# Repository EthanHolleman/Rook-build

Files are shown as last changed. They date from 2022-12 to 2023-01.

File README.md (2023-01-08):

# Rook

This is my fork of the GitHub repo for the [Rook](https://github.com/rolohaun/Rook), a mostly 3D printed CoreXY 3D printer designed
by rolohuan. 



Please see his repo for offical build files and other information. I will be using this repository to
log my build of the printer and store any additional / useful files so that they
can be discovered by others who might want to build this printer.

## Part ordering

Went through the Rook [BOM](https://docs.google.com/spreadsheets/d/1oHDEvndkkvPFOBis4atrHRHK_DMTvttFUFWDg2He6To/edit#gid=0) and
ordered everything specified pretty much using all the provided AliExpress links. 

After I made my order I and looking at the CAD files more closely I realized there was no
hardware specified for attaching the Z axis lead screws to the stepper motors. So I
ended up ordering [this flexible couplings from amazon](https://www.amazon.com/AFUNTA-Flexible-Couplings-Compatible-Machines/dp/B07JL1QYLS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).
In the future I'm guessing equivalent AliExpress couplings will be added to the BOM.

## Software

### Klipper

#### Raspberry Pi

The Rpi hosts the Klipper web interface and API.
I am planning on using Klipper running on a RPi Zero V2. I followed the installation
guide [provided by Rolohaun](https://www.youtube.com/watch?v=OmBIHB9TFgc&t=314s)
pretty much to the letter and got my MainSail interface running without
a problem

#### Klipper and MainSail installation

Follow [part II of Rolohuan's Klipper installation guide](https://www.youtube.com/watch?v=-SYqTW7wJTo). The firmware build will be specific to the mainboard that you have selected. I have decided to
use the SKR E3 V3 because this is the board used by Rolohaun in his build. 

#### Local acccess point

Part of the appeal of the Rook to me is its small size which allows it to be extremely portable.
One challenge I anticipate of bringing this thing around to new places is that
there is no physical interface for controling the machine; everything is depedent on being
able to access the Klipper Mainsail interface. This means that the machine needs to be
connected to wifi so I can use a labtop on the same network 
or other device to access the Mainsail interface. This would be problematic in locations
where there is poor or no access to a local network. 

To get around this I am using a Raspberry Pi Pico W as a local access point. Following
[this guide](https://www.recantha.co.uk/blog/?p=21398) from Michael Horne I got my
Pico hosting a local wifi network. Then when I need to connect to the Mainsail interface
and / or work on the Raspberry Pi Zero running Klipper for the Rook I connect
to this local network from my labtop. 

Code I am using for the access point is below.

```python
import socket
import network
from machine import Pin
import time

ssid = "YOUR SSID"
password = "YOUR PASSWORD"
led = Pin("LED", Pin.OUT)

ap = network.WLAN(network.AP_IF)
ap.config(essid=ssid, password=password) 
ap.active(True)

print("Access point active")
print(ap.ifconfig())

while True:
    if ap.active() == True:
        led.on()
    else:
        led.off()
        
    time.sleep(0.1)
```

I then setup my RPi Zero that is actually running klipper to connect to this network when it boots up.
You can use [this guide](https://www.tomshardware.com/reviews/raspberry-pi-headless-setup-how-to,6028.html) to
configure headlesss SSH access.

### Putting things together

First I started by printed out the main components of the frame using Fusion Filaments PLA Pro +.
The Rook is very sensitive to warped parts so I set the bed temp extra high, used a brim
when printing large frame parts and printed the first layer very slow and very hot.

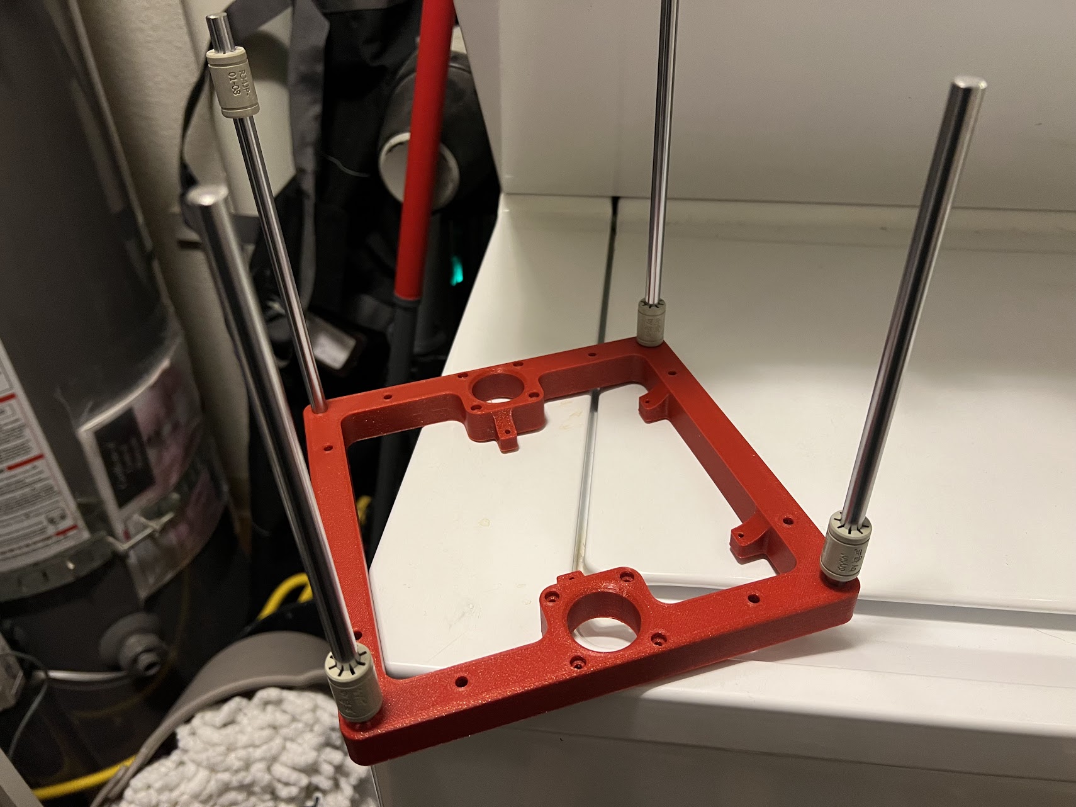
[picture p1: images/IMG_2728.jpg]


With the main frame parts finished I tested the
fit of the linear rods and made sure the delrin
bearings were sliding smoothly along them.



Next I started fitting the rest of the frame and
bed together as well as setting the M3 heat
set inserts using my soldering iron. Everything
went together pretty easily, just make sure all
parts are oriented correctly. I assembled things
backwards at some point. It helps to have the CAD
model open when first putting the frame together
to keep yourself on track as the frame is pretty
symmetrical. 

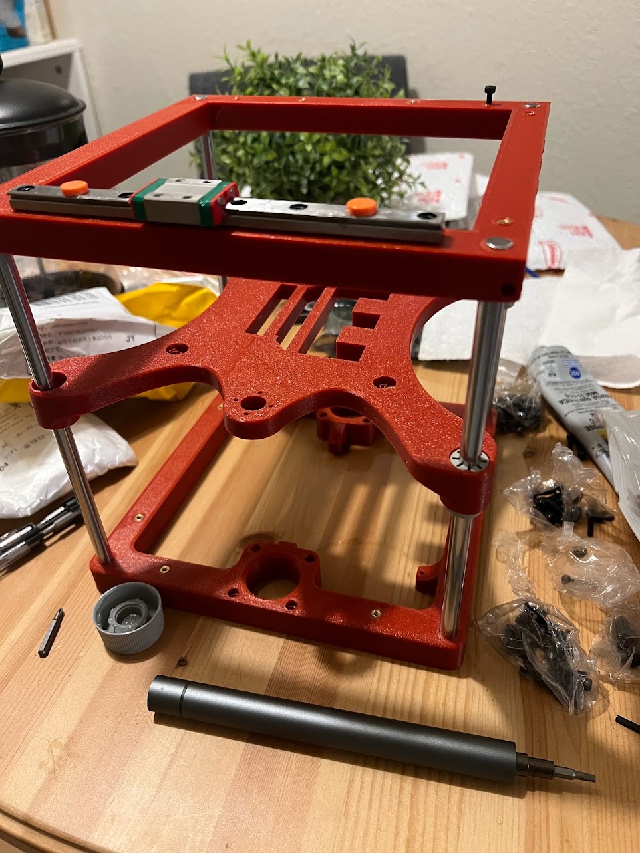
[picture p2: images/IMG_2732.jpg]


I later ended up replacing the bed shown in this
image with the two bearing bedframe that can
be downloaded from Rolohaun's Rook repo. I
found that this bed really does help to reduce
binding on the Z axis. The Rook seems to be very
sensitive to the linear rods not being perfectly
square. The degree of squareness required for a
smooth four bearing set up seems to be difficult
to achieve with 3D printed parts. 

I also lubricated all my linear rods with
Superlube grease by just placing some onto
the rails, moving the rail carriage through the grease
and wiping up the excess. This seemed to work well enough.



Next I printed and assembled the idler towers.
These were a bit tricky to fit everything together.
It helped to sand down the inside area where the washers make contact with the printed plastic with a file. I also used the M5 bolt as a guide to kind of pile the bearings and washers on. As I added more I would screw in the bolt to hold everything in place.

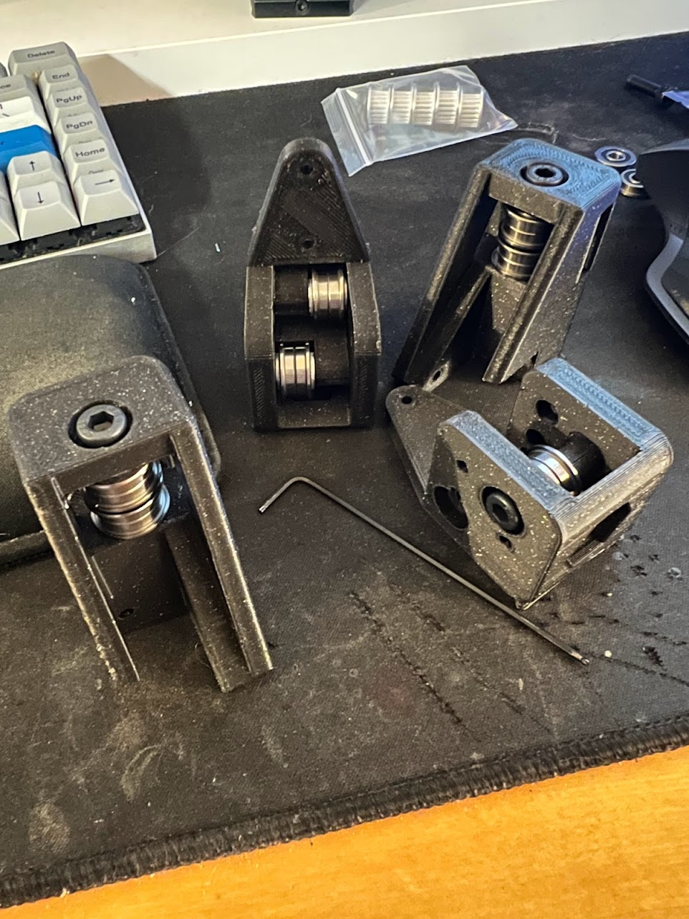
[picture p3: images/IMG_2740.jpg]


With these parts together I then started working on the hot end assembly and the belting. 

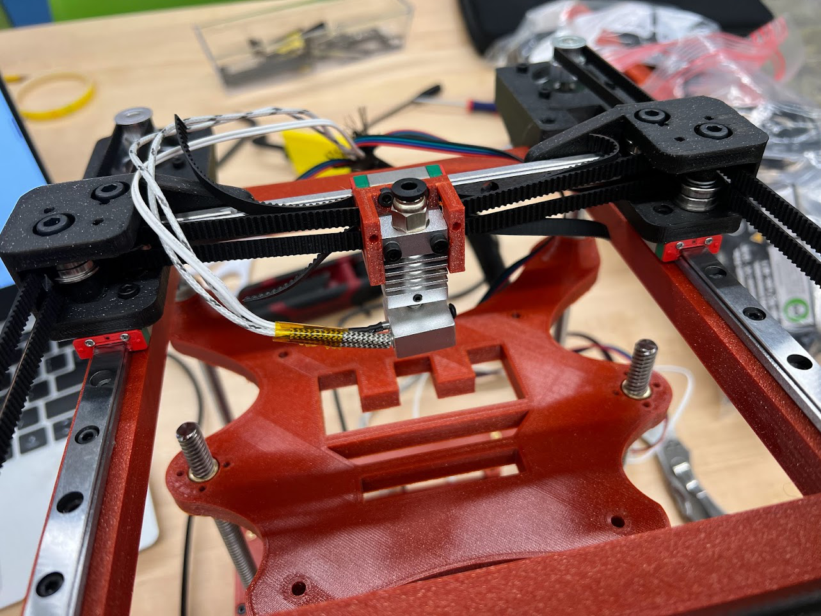
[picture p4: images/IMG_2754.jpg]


I found this image of a general coreXY belting diagram to be very helpful.



After I had the belting figured out I started mounting the bed. I used a 150 mm piece of glass pane I had cut at
a local hardware store with a PEI magnetic build plate as the print surface. 

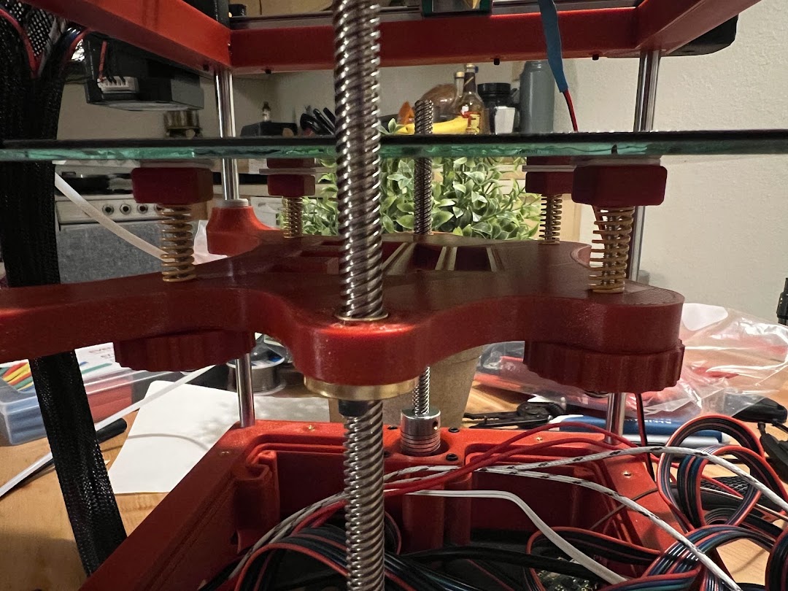
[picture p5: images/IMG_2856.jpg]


I also designed some bed spring tensioning knobs that use the same threaded inserts as the rest of the build.
Double sided tape did not seem like enough to keep the bed attached to the mounts so I just superglued
these to the glass plate.

I then realized that the 40 mm cooling fans I had were too large to fit the hot end mount. So I went into Fusion360 and designed a
mount that would work with my hot end (CR-10 style) and a 40 mm fan. You can download the stl [at this link](https://github.com/EthanHolleman/Rook-build/blob/main/ETH-STLs/X_Carriage-40mm-extra-tall.stl).

Next I moved onto the wiring. I did not want to design a mount for all my individual components so instead I designed an electronics
box that slides into the bottom frame that you can just shove all the wires and computers into and then seal up and never think
about again.

Something to note about this electronics box
is that it needs to be installed *before* you
mount the Z axis motors and the legs because
it will be obstructed and difficult / impossible
to push up from the bottom of the frame otherwise.

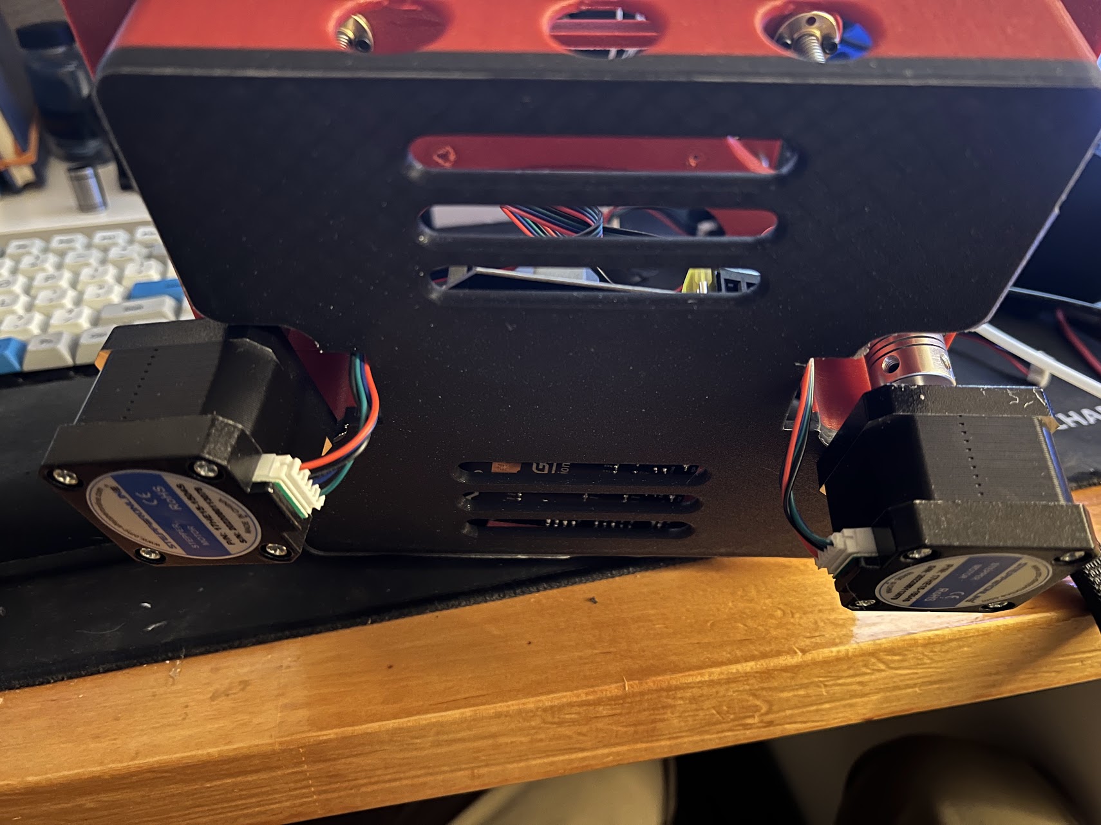
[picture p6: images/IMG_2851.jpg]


Wires for the Z axis motors can be routed
through the holes adjacent to them. 

Everything fits I promise!

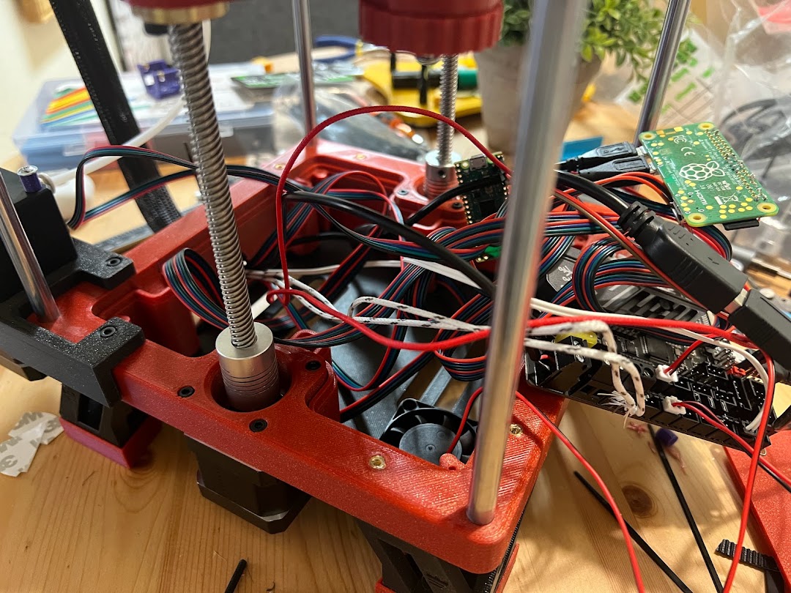
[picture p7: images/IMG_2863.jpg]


After verifying that everything seemed to be working I wired in the cooling fan, did some additional cable management and then sealed everything up using the lid I designed for the electronics box. I also threw in another 40 mm
fan into the enclosure in an attempt to help 
keep things a bit cooler in there. The links for both the box and lid are listed below.

- [Electronics box stl](https://github.com/EthanHolleman/Rook-build/blob/main/ETH-STLs/electronicsBox.stl)
- [Electronics box lid stl](https://github.com/EthanHolleman/Rook-build/blob/main/ETH-STLs/electronicsBoxLid.stl)

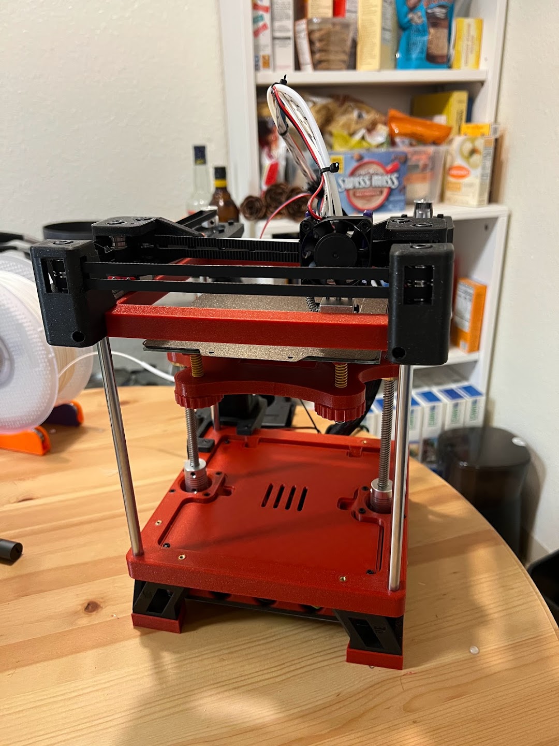
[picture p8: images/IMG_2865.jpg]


The only thing left to do at that point was to mount the part cooling fan and test everything out! After leveling the bed and fooling around
with the Z offset in Klipper I was able to print a calibration cube.

And with that my Rook build was complete. I really enjoyed putting this machine together and feel like I have a much deeper understanding of
3D printers and the mechanics that allow them to function.

[Video of first print](https://www.youtube.com/watch?v=ggh4lNVPjAo)

I posted my Rook to Rolohan's discord server and officially received serial number 27! So this is the 28th Rook to exist in the world (counting starts at 0). Overall this was a very fun project and I would
recommend Rook to anyone looking to try out building
a printer from scratch but does not want to shell
out the cash for a Voron type build. The mostly
3D printed design and relatively low cost to build
(mine came in at around 300 USD when all was said
and done but that could definitely be powered due to
some purchasing inefficiencies on my end) make this
build low risk. An added bonus is that the small
size and light weight means that you can fit
this guy into your second carry on bag no problem.
I fly home for Christmas with mine without any
issue!

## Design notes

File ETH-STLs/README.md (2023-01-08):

# Custom parts

As part of putting Rook together I designed a few parts either to work around
problems I had or to suit my needs for the printer better. They are described
below.

## `electronicsBox.stl` and `electronicsBoxLid.stl`

This is a box and lid that fits into the bottom part of the stock Rook base.
It has pass-throughs for cables so instead of designing mounts for all your
hardware you can just jam everything into this box. I beleive other Rook builders
have published electronics boxes but they do not use the stock bottom frame. 
I had already printed the stock frame so I wanted an electronics box that
would work with that.

## `ExtruderBottomText.stl`

This is a modified X axis motor mount that you can attach to the back left
of Rook to mount the extruder motor cleanly. Mounting the extruder motor at
the bottom of the machine helps to lower the center of gravity.

## `X_Carriage-40mm-extra-tall.stl`

The 40 mm fan was too large to fit on the stock hot end mount so I
modified it to fit this fan size. Seems to work well.

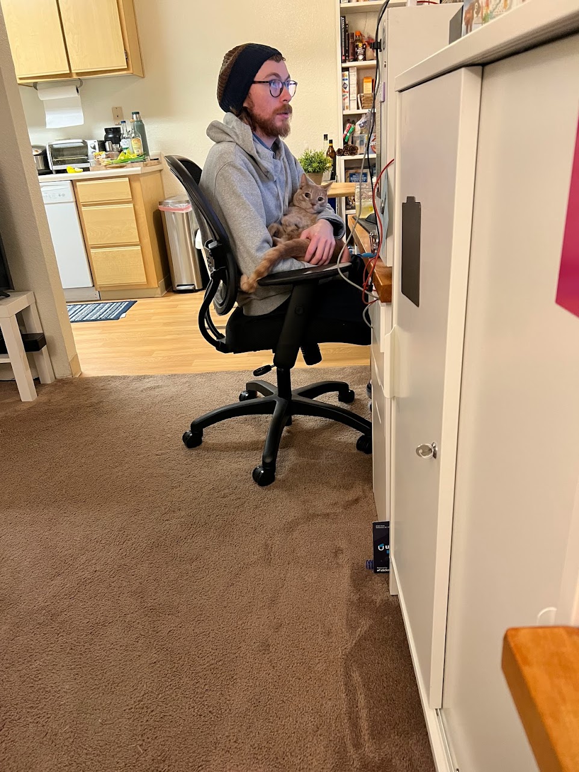
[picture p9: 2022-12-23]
images/55D79FF7-644D-44E7-BA7D-22746BB70248.jpg

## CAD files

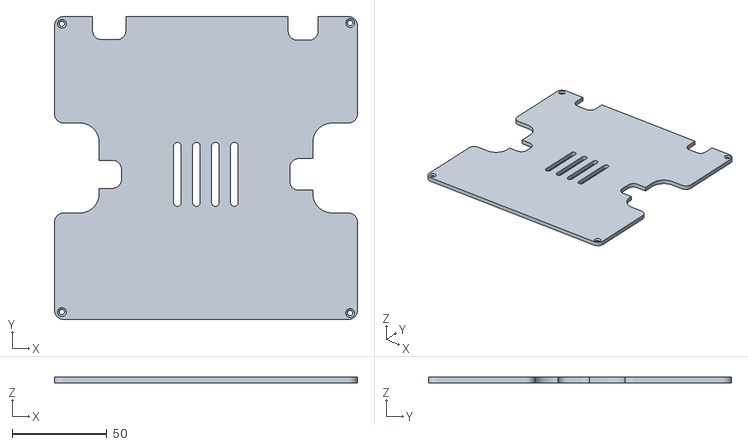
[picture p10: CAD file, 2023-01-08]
ETH-STLs/electronicsBoxLid.stl
159.6 x 159.6 x 3.00

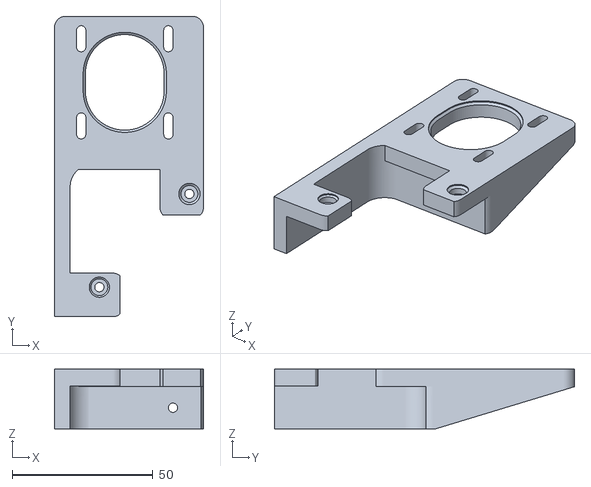
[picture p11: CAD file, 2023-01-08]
ETH-STLs/ExtruderBottomText.stl
53.0 x 106.9 x 21.2

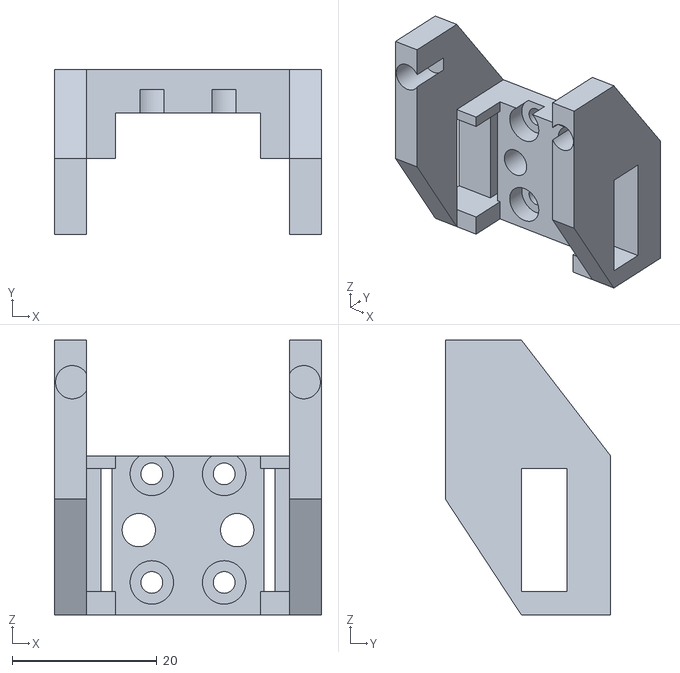
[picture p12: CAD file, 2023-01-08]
ETH-STLs/X_Carriage-40mm-extra-tall.stl
36.9 x 22.8 x 38.0

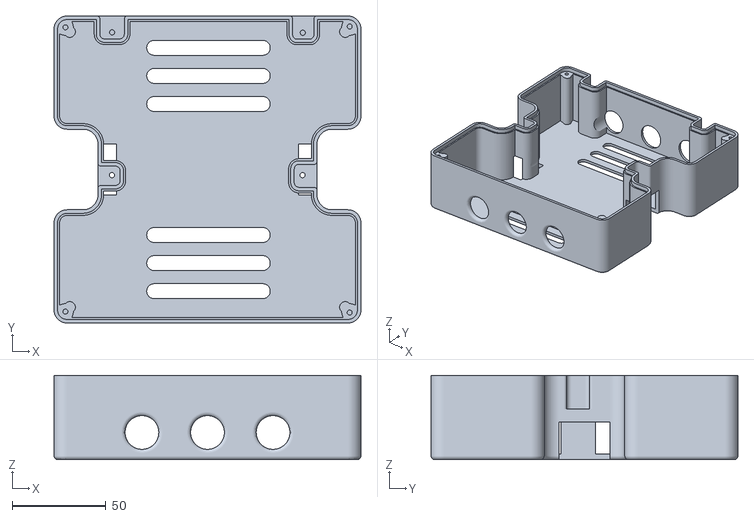
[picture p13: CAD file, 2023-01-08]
ETH-STLs/electronicsBox.stl
164.0 x 164.0 x 45.0

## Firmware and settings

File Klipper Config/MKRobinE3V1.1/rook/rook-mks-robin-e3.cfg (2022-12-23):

# This file contains common pin mappings for MKS Robin E3 boards. To
# use this config, the firmware should be compiled for the STM32F103.
# When running "make menuconfig", enable "extra low-level
# configuration setup", select the 20KiB bootloader, and serial (on
# USART1 PA10/PA9) communication.

# Note that the "make flash" command does not work with MKS Robin
# boards. After running "make", run the following command:
#   ./scripts/update_mks_robin.py out/klipper.bin out/Robin_e3.bin
# Copy the file out/Robin_e3.bin to an SD card and then restart the
# printer with that SD card.

# MKS Robin E3 has onboard TMC2209. This config can also be used for
# MKS Robin E3D if equipped with TMC2209 stepper drivers.

# Please note pin name change for stepper Z for v1.1 of the boards.

# See docs/Config_Reference.md for a description of parameters.

# File edited for Rook configuration Ethan Holleman 12/6/22
# Original downloaded from 
# https://raw.githubusercontent.com/Klipper3d/klipper/master/config/generic-mks-robin-e3.cfg
[include mainsail.cfg]

[stepper_x]
step_pin: PC0
dir_pin: PB2
enable_pin: !PC13
microsteps: 64  # 16 -> 64
rotation_distance: 40
endstop_pin: tmc2209_stepper_x:virtual_endstop  # from Rook config
position_endstop: 120  # 0 -> 120
position_max: 120  # 165 -> 120 
homing_speed: 40  # 50 -> 40

[tmc2209 stepper_x]
uart_pin: PC7
run_current: 0.800
uart_address: 0  # from Rook
stealthchop_threshold: 0  # 99999 -> 0
interpolate: False
sense_resistor: 0.110  # added from Rook
driver_SGTHRS: 90  # added from Rook
diag_pin: ^PA12    # Set to MCU pin connected to TMC DIAG pin
driver_SGTHRS: 90 # 255 is most sensitive value, 0 is least sensitive

[stepper_y]
step_pin: PC2
dir_pin: PB9
enable_pin: !PB12
microsteps: 64  # 16 -> 64
full_steps_per_rotation: 200  # added from Rook
rotation_distance: 40
endstop_pin: tmc2209_stepper_y:virtual_endstop  # from Rook
position_endstop: 120   # 0 -> 120
position_max: 120  # from Rook
position_max: 120  # 165 -> 120
homing_speed: 40  # 50 -> 40
homing_retract_dist: 0  # from Rook


[tmc2209 stepper_y]
uart_pin: PD2
run_current: 0.800
uart_address: 2  # from Rook
sense_resistor: 0.110  # from Rook
stealthchop_threshold: 0  # 999999 -> 0
interpolate: False   # from Rook
diag_pin: ^PA11
driver_SGTHRS: 70  # from Rook


[stepper_z]
step_pin: PB14 # PC14 if using board v1.1
dir_pin: !PB15 # !PC15 if using board v1.1
enable_pin: !PB8
microsteps: 64  # 16 -> 64
homing_retract_dist: 8  # from Rook
rotation_distance: 8
endstop_pin: ^PC6
position_endstop: 112.8  # 0 -> 112.8
position_max: 211500  # 200 -> 115
homing_speed: 10  # from Rook

[tmc2209 stepper_z]
uart_pin: PC12
run_current: 0.650
uart_address: 1  # from Rook
stealthchop_threshold: 0  # 999999 -> 0
sense_resistor: 0.110  # from Rook
interpolate: False
diag_pin: ^PC6
driver_SGTHRS: 70

[extruder]
step_pin: PB4
dir_pin: PB3
enable_pin: !PB5
microsteps: 64  # 16 -> 64
rotation_distance: 22.43   # 33.500 -> 22.43
nozzle_diameter: 0.400
gear_ratio: 3:1  # using 3:1 dual geal BMG clone for my setup
filament_diameter: 1.750
heater_pin: PC9
sensor_type: EPCOS 100K B57560G104F
sensor_pin: PA0
control: pid   # These 4 lines comment out in Rook config
pid_Kp: 21.527 # but Klipper threw error saying it wanted them
pid_Ki: 1.063
pid_Kd: 108.982
min_temp: 0
max_temp: 250
pressure_advance_smooth_time: 0.040


[tmc2209 extruder]
uart_pin: PC11
run_current: 0.800
stealthchop_threshold: 0  # 999999 -> 0
uart_address: 3  # from Rook
sense_resistor: 0.110  # from Rook
interpolate: False

[fan]
pin: PA8

#[heater_bed]
#heater_pin: PC8
#sensor_pin: PA1
#...

#[bltouch]
#sensor_pin: ^PC6
#control_pin: PA3
#...

#[filament_switch_sensor my_sensor]
#switch_pin: PB10
#...
# https://github.com/Klipper3d/klipper/issues/2339
[mcu]
serial: /dev/serial/by-id/usb-1a86_USB_Serial-if00-port0

restart_method: command

[printer]
kinematics: corexy
max_velocity: 300
max_accel: 10000
max_z_velocity: 10
max_z_accel: 100

# EXP1 / EXP2 (display) pins
[board_pins]
aliases:
    # EXP1 header
    EXP1_1=PC3, EXP1_3=PA4, EXP1_5=PA6, EXP1_7=PC4, EXP1_9=<GND>,
    EXP1_2=PC1, EXP1_4=PA5, EXP1_6=PA7, EXP1_8=PC5, EXP1_10=<5V>,
    # EXP2 header
    EXP2_1=PB14, EXP2_3=PB11, EXP2_5=PB0,  EXP2_7=PC10,  EXP2_9=<GND>,
    EXP2_2=PB13, EXP2_4=PA15, EXP2_6=PB15, EXP2_8=<RST>, EXP2_10=<NC>,
    # CR_EXP3 header - additional header dedicated to Creality Ender 3/5 stock screens
    CR_EXP3_10=<5V>, CR_EXP3_8=PA4, CR_EXP3_6=PA6, CR_EXP3_4=<RST>, CR_EXP3_2=PC3,
    CR_EXP3_9=<GND>, CR_EXP3_7=PA5, CR_EXP3_5=PB0, CR_EXP3_3=PB11,  CR_EXP3_1=PC1

# If you're using this board to replace stock Creality board, connect display to EXP3
# and use this display config
#[display]
#lcd_type: st7920
#sid_pin: CR_EXP3_8
#cs_pin: CR_EXP3_7
#sclk_pin: CR_EXP3_6
#encoder_pins: ^CR_EXP3_5, ^CR_EXP3_3
#click_pin: ^!CR_EXP3_2
#
#[output_pin beeper]
## pin: EXP1_9
#pin: CR_EXP3_1

# See the sample-lcd.cfg file for definitions of common LCD displays.

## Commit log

2022-12-06 start klipper notes
2022-12-06 start working on klipper Rook MKS config
    [generic-mks-robin-e3.cfg, rook-mks-robin-e3.cfg]
2022-12-23 update board
2023-01-08 add first print link
